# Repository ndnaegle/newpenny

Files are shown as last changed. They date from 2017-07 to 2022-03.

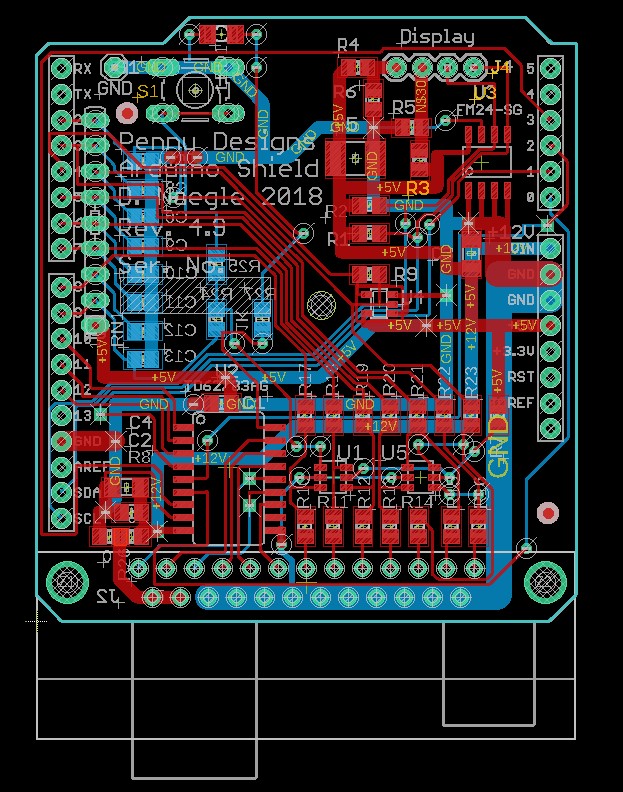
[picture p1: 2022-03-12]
Docs/PennyMan_Ard_R3_Shield_v9.5_all_layers.jpg

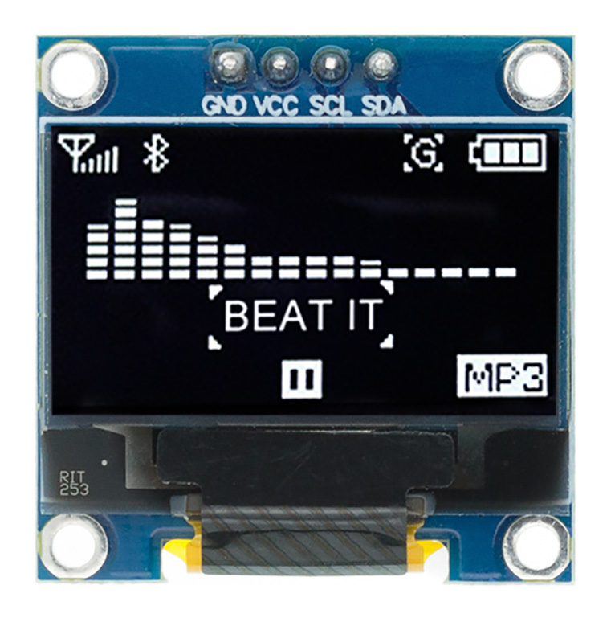
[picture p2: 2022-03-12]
Docs/SSD1306_I2C_DisplayModule.jpg

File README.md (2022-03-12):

# newpenny
This is an Arduino Shield to interface an Arduino to a souvenir making machine.  

The shield contains signal conditioning to give the Arduino more ESD protection as a controller  for the penny press.  

The shield also contains an output level shifter to allow the Arduino to control solid-state relays  that require 12V control inputs.  

The shield also contains a 128x64 pixel display as a debugging aid, and a non-volatile serial memory for storing operational and debug data.  

The shield could serve as a general-purpose I/O conditioning module along with non-volatile memory that could allow the Arduino to retain its
operational state through power failures, by means of appropriate software.

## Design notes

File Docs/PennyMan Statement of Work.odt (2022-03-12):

PennyMan Control Software Description

David Naegle

11 June 2017

The PennyMan machine is a roller press with dies in it that turns a US penny into a souvenir by imprinting it with images or impressions that are typically mementos of the location in which the penny machine resides.

The machine is electrically operated, and is capable of making any one of four impressions by means of a roller die containing four different images located at 90-degree offsets around the circumference of the roller die. The machine works are enclosed in a protective case containing clear windows so that the machine can be observed in operation; the user experience consists in observing the machine making a souvenir for the user, as well as the souvenir itself.

A description of the machine operation follows.

When active, the machine waits for coins to be inserted. The mechanical coin feed ensures that exactly 51 cents, in the form of two quarters and a penny, are required to activate the machine. Once these coins are inserted, the machine prevents any other coins being inserted until the present operation is completed.

The machine waits for the user to select one of 4 impressions to be made on the penny, by means of 4 switches with illustrations of each of the 4 choices for impressions.

Once the user has made a selection, the machine starts the roller mill. Magnetic sensors sense the position of the die, and drop the penny into the mill when the roller die is appropriately positioned for the impression selected by the user in the previous step.

When the penny has been imprinted with the selected image and transformed into souvenir form, it drops down a chute to be picked up by the user.

The machine keeps the roller mill turning until the magnetic sensors indicate it is once again in the “home” position (half-way between impressions 1 and 4). At this point the mill motor is shut off, the coin slot is re-enabled to accept coins, and the cycle starts over, with the machine waiting for another set of coins to be inserted.

The control for the machine comes from an Arduino processor board, equipped with a “shield” which provides connectivity and compatibility with the connectors and wiring harness of the penny machine.

The shield board also provides electrostatic protection and switch “de-bouncing” for signal inputs, as well as voltage level translation on outputs. Outputs level translation is needed to allow the Arduino 3.3V or 5.0 V output signals to drive 12 V solenoids and the motor relay for the machine.

A table of inputs and outputs follows:

Signal | Name | Arduino Pin | | Direction | Notes
1 | Go/No-Go | P0.0 | | In | Go = 0, Halt = 1
2 | Coin Accept | P0.1 | | In
3 | Die #4 | P0.2 | DB25.6 | In
4 | Die #3 | P0.3 | DB25.5 | In
5 | Die #2 | P0.4 | DB25.4 | In
6 | Die #1 | P0.5 | DB25.3 | In
7 | 90-Degree | P0.6 | DB25.2 | In
8 | Home | P0.7 | DB25.1 | Out
9 | Cycle Start | P1.0 | DB25.12 | Out
0 | Solenoid | P1.1 | DB25.10 | Out
11 | Motor Run | P1.2 | DB25.9 | Out
12 | Counter | P1.3 | DB25.7 | Out
13 | | | | Out
14 | | | | Out
15 | | | | Out

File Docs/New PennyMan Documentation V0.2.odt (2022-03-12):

The (Arduino) PennyMan Shield Documentation

D. Naegle

31 October, 2018

1. OLED Display

The PennyMan Arduino interface shield contains provisions for an inexpensive 128x64-pixel Organic Light-Emitting Diode (OLED) display (0.96” SSD1306 128x64 I2C Serial 4Pin Arduino Display Module, available from multiple sellers on eBay, or from Adafruit Industries). Its purpose is to provide continuous indications of what the PennyMan controller is doing (what is the current state of the machine) and the current values of the input and output signals to the PennyMan controller. The PennyMan Shield design accommodates 2 versions of the display module, which differ in the placement of their VCC and GND pins. For VCC on the left-most pin, stuff R4 and R5. For GND on the left-most pin, stuff R3 and R6.

2. OLED Display is optional

Use of the OLED display is optional; the PennyMan Arduino interface shield operates correctly without the shield in place.

CAUTION: Do not plug or unplug the OLED display with power applied to the PennyMan controller. Unplug the power connector to the Arduino processor board, and wait a few seconds before plugging or unplugging the OLED display.

3. Software Interface

The OLED display is accessed through the I2C serial interface provided by the AdaFruit_SSD1306 library.

4. Layout and format of the Display

The display has 3 modes of operation:

· Startup Screen

· Runtime Screen

· Debug Console

These are described as follows

4.1 Startup Screen

The Startup Screen has the banner ‘Pennyman!’, followed by the software revision, optionally followed by a 5-second count-down indicator. The time-out is provided so that the user can get into the Debug Console, in the case that the non-volatile log chip is present on the PennyMan Arduino interface shield. If there is no log chip installed, there will be no count-down; the Startup Screen will be replaced by the Runtime Screen after a few seconds. See Section 4.3, Debug Console, for further information.

4.2 Runtime Screen

The Runtime Screen has 3 lines: Current State, I/O State, and time in current state. The top line indicates the current state of the machine. These are listed below:

State Message Visible in OLED Display | Comment/Explanation
"Start" | Startup State; doesn’t last long enough to be seen on the OLED display. This state sets all output to sane (inactive) values and moves to “Wait for Home”
"Wait for Home" | Runs the Motor, waits for the Home sensor to be active. When Home is sensed, the coin press is in the proper position to begin; this state moves to “Wait for Coin”
"Wait for Coin" | Waiting for the user to insert a penny and quarters to initiate creation of a souvenir. Only in this state, is the Coin-insert mechanism is enabled (Upper Solenoid activated). This is shown by the ‘L’ being a black letter on a white background. (‘L’ stands for ‘Lift Red lever’.) When coins are inserted, the state moves to “Wait for Button”
"Wait for Button" | Wait for the user to select which stamp to impress on the penny. When this selection is made, the state moves to “Position Stamp”
"Position Stamp" | This is a timing state. The Motor is run, and the 90-degree sensor is counted until the press is in the proper position for the user’s selected stamp. At this point, the state moves to “Coin Drop”
"Coin Drop" | Lower Solenoid is activated to drop the penny into the press. Motor continues running in this state. This state lasts for 1 second, then the state moves to “Wait for Finish”
"Wait for Finish" | Motor continues running in this state. This state lasts for 5 seconds, to insure that the souvenir is released from the press into the output chute where the user will pick it up. NOTE: running the motor in this state may cause the press to advance past the ‘Home’ position. This is OK. After 5 seconds, the state moves to “Start”, resetting all outputs inactive and immediately going to “Wait for Home”. As mentioned above, the press may make an entire, extra revolution before the machine is once again in “Wait for Coin” state.
The states below are not part of normal operation; they should not be seen on the Display.
"Invalid" | Software sets the state to ‘Invalid’ before immediately starting the State Machine in the ‘Wait For Home state’ This is just software housekeeping, so the State variable has a known value as soon as possible after the machine powers up.
"Shutdown" | Software defines this state, but it is not used in normal operation. There is no legal way to get to this state. All outputs are set to safe (inactive) values in this state, as part of an “emergency recovery” strategy. From this state, the state goes to “Wait Forever”
"Wait Forever" | This state is intended to trap a runaway machine sequence into a safe, persistent state. As the name implies, we’re stuck in this state until the machine is reset or powered down. If you see this on the Display, you know the machine has been trapped from an unusual and unintended mode of operation. It would be useful to look at the Log, if possible. (See Section 4.3 for instructions on entering the Debug console.)
"Reset" | This was intended to be similar to the “Shutdown” sequence; it attempts to clear the Display, set outputs to safe values, and sets the Watchdog Timer, which will initiate a system reset. It apparently never worked, and is probably not needed. The board will emerge from reset as described above, in “Start”.
"Unknown!" | If the State has any value other than those enumerated above, the Display should show “Unknown!”. Since this is not expected, it should never be seen. It’s unknown if this state would persist on the “Display”. It’s documented here for completeness’ sake. If you see this, you should probably attempt to dump the log, and read the PennyMan source code to figure out what might have happened. Or forget it and move on. Perhaps it would be a good idea to replace the Arduino, the PennyMan shield board, or both, if an unusual state persists.

4.3 Debug Console

The Debug Console must be activated during the 5-second count-down period in the Startup Screen. This is done as follows:

4.3.1 Connect the Arduino to a PC running the Arduino Integrated Development Environment (IDE), using a USB cable.

4.3.2 Under the ‘Tools’ tab in the Arduino IDE, you’ll find a ‘Port’ tab. Select the appropriate COM port (e.g. COM1, COM2, etc.) If you select the wrong COM port, step 4.3.3 will be unsuccessful; you’ll get a warning message about the selected port not being found. Come back to this step and select another COM port.

4.3.3 Under the ‘Tools’ tab, select ‘Serial Monitor’. Look for any error messages that appear in the bottom pane of the Arduino IDE window, indicating failure to open the Serial Monitor with the correct COM port.

4.3.4 Upon successfully opening the Serial Monitor window, select ‘115200 baud’ in the serial speed control pane at the bottom of the Serial Monitor window. The Arduino IDE may remember this from a previous session, so it may not be necessary. NOTE: opening the Serial Monitor window resets the Arduino hardware, forcing it to start from scratch. The Log file, if any, will be unaffected by resets. See section X.X for more information on using the log file.

4.3.5 Position the PC’s cursor in the uppermost pane of the Serial Monitor window (to the left of the ‘Send’ button) and type a ‘d’ but DON’T HIT RETURN yet.

4.3.6 Press the reset button on the Arduino board (NOT the pushbutton on the PennyMan Arduino interface shield board (the top board in the stack). The Arduino reset button is on the lower (main Arduino) board, next to the USB connector. This will initiate the Startup screen and the 5-second time-out period.

4.3.7 Hit ‘Enter’ (or ‘Return’ depending on the labeling of your PC keyboard) or click ‘Send’ on the Serial Monitor window within the 5-second time-out. Either of these actions will send the previously typed ‘d’ to the Arduino board. The OLED Display will show “Debug console running’. The Serial Monitor should also show a list of commands that can be typed from the top pane of the Serial Monitor in Debug mode, to manage the Log file.

4.3.8 In the Debug Console, there are 3 commands, ‘d’, ‘c’, and ‘x’. ‘d’ dumps the log file to the Serial Monitor. Dumping the log file does not erase it. However, you may wish to preserve the log file in a human-readable form, by selecting the dumped text from the Serial Monitor central pane, copying it (with ‘ctrl-C’) and pasting it to your favorite text editor. From there, the file can be saved or processed as needed. ‘c’ clears the log file. There is no recovering from this! ‘x’ exits Debug Mode and boots back into the Runtime mode and screen.

5. Using the Serial Monitor.

If connected to a PC via USB to the Arduino IDE with a Serial Monitor opened as described above, the PennyMan Arduino Controller prints the same messages to the Serial Monitor as to the Log File. These messages have the following format: <timestamp> of the form hours.minutes.seconds.milliseconds, followed by the separator ‘->’, followed by a description of actions occurring at that timestamp. There may be multiple lines of output. It’s not completely clear which timestamp such unlabeled lines are associated with. However, if there are multiple un-timestamped lines, they all occurred essentially simultaneously, some time after the nearest-preceding time stamp, and before or at the subsequent time stamp. NOTE: the timestamp does not come from the Arduino; it’s the PC’s system time. Showing the Timestamp can be controlled by checking or un-checking the ‘Show Timestamp’ box at the bottom of the Serial Monitor. Similarly, ‘Autoscroll’ affects the screen by being checked or unchecked. In general, the default settings at the bottom of the Serial Monitor are best (except for the Baud rate, which must be manually set to 115200 baud in order to get non-gibberish messages to appear on the Serial Monitor)

It may be useful to clear the Serial Monitor window; this may be done by clicking the ‘Clear output’ button at the lower-right of the Serial Monitor screen.

NOTE: It is possible (and very convenient) to exercise the Arduino & PennyMan shield by connecting them to the PC with the USB cable (no separate 12-volt power supply is needed). You don’t need to connect the DB-25 connector to the PennyMan wiring harness, either. You can simulate the inputs using the Serial Monitor, by typing a character into the Serial Monitor, and hitting the ‘Send’ button or simply hitting ‘Enter’ on the keyboard. NOTE: not all characters will be recognized in all states. Carefully read the table below, to determine the characters expected (and the only ones allowed) in any given state.

NOTE: although it is possible to program the PennyMan software into an Arduino without a PennyMan shield board attached, (see section 6 for programming instructions) the PennyMan program will NOT run reliably on the Arduino without a PennyMan shield board attached. This is because the pull-up resistors which keep the input signals at known (sane) levels are on the PennyMan shield; without the shield installed, the inputs are “floating”. They may be High (inactive), Low (active) or anywhere in between. Random cosmic rays can change the state of floating input pins, and the Arduino will interpret the floating inputs in ways that lead to chaotic operation. Save yourself a lot of confusion; always us a PennyMan shield, even when you’re only connected to the PC.

State Message Visible in OLED Display | Legal/Expected Characters from Serial Monitor
"Start" | n.a. (no user input expected in this state)
"Wait for Home" | h
"Wait for Coin" | c
"Wait for Button" | 1, 2, 3, or 4
"Position Stamp" | 9. (you’ll need to send a ‘9’ 1, 2, 3, or 4 times, depending on which button you selected, above.)
"Coin Drop" | n.a. (no user input expected in this state)
"Wait for Finish" | n.a. (no user input expected in this state)
The states below are not part of normal operation; they should not be seen on the Display. If you get any of the states below, it may indicate an Arduino board that is beginning to fail; replace it and try again.
"Invalid" | n.a. (no user input expected in this state)
"Shutdown" | n.a. (no user input expected in this state)
"Wait Forever" | n.a. (no user input expected in this state)
"Reset" | n.a. (no user input expected in this state) Note, however, that opening the Serial Monitor causes a reset, as does changing the baud rate (e.g., to something other than 115200 and changing it back to 115200 again.)
"Unknown!" | n.a. (no user input expected in this state)

6. Programming the Arduino.

Obtain the PennyMan source code from GitHub as follows:

Go to

https://github.com/ndnaegle/newpenny

There are 2 directories under this project, Docs and main. Docs contains design information and documentation, including this file. main contains the Arduino code for the project.

The use of GitHub is beyond the scope of this document, but there are plenty of tutorials on the Web.]

Further note: The newpenny Arduino sketch (Arduino programs are called 'sketches') requires, in addition to all the files in the newpenny GitHub repository, the AdaFruit SS1306 display libraries and the AdaFruit graphics library. To get the SS1306 library, go to this site: https://github.com/adafruit/Adafruit_SSD1306 and click 'Clone or Download'. Select 'Download ZIP file'. That should put a copy of the Zip file in your Downloads directory if you're running Windows. The process is similar for MacOS. To get the AdaFruit Graphics library, go to this site: https://github.com/adafruit/Adafruit-GFX-Library and click 'Clone or Download'. Select 'Download ZIP file'. That should put a copy of the Zip file in your Downloads directory if you're running Windows. Jon modified the FRAM library from AdaFruit, but didn't debug it sufficiently to recognize any FRAM but the ones from Fujitsu. I think a better library is available here: https://github.com/adafruit/Adafruit_FRAM_I2C although some coding work would have to be done to insure the routines Jon wrote for his library can be replaced by those in FRAM_I2C. The advantage is that much more testing has been done with FRAM_I2C for supporting many types of FRAM.

Look at the documentation for the Arduino IDE about loading libraries. Basically, from inside the Arduino IDE, you can load additional libraries. There is a dialog for navigating to the ZIP file containing the library and opening it. Once the Arduino IDE has opened the ZIP file containing the library, it will be accessible to programs wishing to use it; you won't get compile errors complaining about missing libraries.

Once you have the PennyMan source on your PC (mine is at C:\Users\Naegle\Documents\GitHub\newpenny) you start up the Arduino IDE (downloadable from the Web; google for details), navigate to …\GitHub\newpenny, and open main.ico. This should give you the whole source. You can compile the code to check it by clicking on the check-mark box in the upper-left of the Arduino IDE. You can compile and upload the code to a connected Arduino board (see above for connecting the board with a USB cable) by clicking on the right-arrow button in the Arduino IDE. Note any diagnostic messages in the bottom of the IDE; they will tell you if you succeeded in programming the Arduino, and if not, what may have gone wrong. Full instructions on compilation and uploading are beyond the scope of this document, but are well-documented on the Web.

7. Weird Stuff it’s well to watch.

7.1 Pin D4 (Coins Accepted) was hard to “pull down” (bring to an active, (LOW) state) on the Arduino board. I tried a couple of different Arduinos, with the same result, but never found out the reason why this input didn’t behave like the others. I used a strong buffer the 74AHC1G125, to force the Arduino D4 pin LOW when the coin drop was active. I have designed in a “stuffing option” to the shield board, such that the 74AHC1G125 buffer can be eliminated and a zero-ohm bypass resistor installed (R9), which will be cheaper and SHOULD work correctly. I tried this experiment with the latest (Rev 4.8) version of the PennyMan shield, and the buffer is still required. NOTE: DO NOT install BOTH R9 and the 74AHC1G125, install one or the other. Next step: try explicitly setting Arduino pin D4 as an INPUT. Jon took advantage of the published behavior of the Arduino IDE to set pins to be inputs by default. But what if pin D4 is set up strangely. (No Google searching revealed any problems with default-input behavior specific to pin D4, and Jon maintains it should be a regular input. I've minutely searched the schematics and examined the Arduino board layout to find if there's anything else connected to D4 that would change its behavior. Still a mystery, so for now, we'll rely on the fact that we have the buffer, and hope its use doesn't stress the Arduino pin. Somewhere a lot of current is getting shorted to ground by the 74AHC1G125 buffer. Fortunately, the buffer is only active for a second or so (for as long as the coin slide is pushed in), so the stress is not continuous over time.

7.2 I had hoped to increase the flexibility of the PennyMan shield (for other projects) by including a mechanism to bring +12V out of the DB-25 connector. To do this I “stole” a couple of ground pins on the DB-25, making them programmable as +12V or “floating”. However, I found that the Upper Solenoid solid state relay uses a ground on the harness which is connected to one of the DB-25-pins I “stole”. Therefore, it is necessary to connect these pins to ground. This may be done on the board, with a zero-ohm surface-mount resistor (R8) placed so that it shorts the output pins to the ground side of C2. This is not really ideal, however. An easier way is to simply take a short piece of wire and short DB25 pins 25 and 24 to pin 23.

7.3 The SSD1306 OLED display is available with two different pin placements for +5V and GND. In order to accommodate the use of both types (and thus keep costs down on the board, by buying whichever version happens to be cheaper at the moment) I have designed zero-ohm resistors (R3, R4, R5, R6) to connect the two power pins on the OLED display to the appropriate power and ground. Two of these resistors MUST be left un-stuffed, in order to avoid a power-to-ground short circuit, which will damage both the PennyMan Shield and the Arduino board. Plugging in a wrong-style OLED display will also damage the display and maybe the shield and Arduino. It might be prudent to select one or the other type of display, so that you don’t have to be so careful to mate the proper display with the proper placement of these resistors.

7.4 The pushbutton on the Shield was intended as an additional, generic input. It is currently unused, but goes to an Arduino input (D9) which could be defined in inputs.h and used in some way. But without writing software, this pushbutton does nothing, and could be left un-stuffed on the board to reduce cost and speed up assembly of the shield.

7.5 I have put a ground pin close to the pushbutton switch. This is a convenience for debugging the board; it’s often handy to have an easy place to ground an oscilloscope probe or multi-meter probe, when making measurements. It is not really needed during normal operation, and could be eliminated without any ill effect (until you need to connect a ground to the board when you’re debugging something. At that point, you could do a field-soldering job and put in a wire or a pin in that location.)

7.6 There are several flavors of FRAM log chip that all fit the pin-out of the board. The FRAM_I2C.cc module attempts to read the size of the chip installed, and sets up the FRAM according to the size it finds. However, the cheapest versions of the FRAM chip (24C04) do not have a manufacturer’s ID like some of the more modern (more expensive) chips. The Fujitsu 256K chip costs about $4-6, whereas the Cypress Semi 24C04 costs about a dollar. Currently the FRAM_I2C module does not correctly set up the 24C04. This leads to strange behavior in Debug Mode, when the software believes there’s a log chip, but it doesn’t work correctly because it’s not properly set up, because it wasn’t recognized because it doesn’t have a manufacturer’s ID. We can solve this by only using the Fujitsu parts. But it’s not a very elegant solution.

7.7 The current implementation of the FRAM dedicates the entire chip to the Log file. There ought to be a way of reserving the first few locations in the chip for use as counters. This would involve some changes (probably minor) to the way the log addressing is done: set the initial log pointer to just above the reserved space for the counters, set the wrap-around routine to respect the reserved locations and avoid clobbering them when it wraps the log address around. And, of course, there needs to be some new FRAM routines written to use the reserved locations as Counters. NOTE: there is no (legacy) counter function implemented on the latest (Rev 4.8) version of the PennyMan shield.

7.8 There will need to be some minor changes to the FRAM_I2C code to recognize that the Log chip is absent (un-stuffed), in order to properly disable the logging and the debug console when no chip is present. The logging FRAM chip is the most expensive one remaining on the PennyMan shield board, and it’s not required for normal operation of the PennyMan system, according to Kristen and Brett.

  9. I made a couple of designs for latching the “red lever” (coin-accept enable) so that the upper solenoid (coin-accept enable) wouldn't have to be continuously activated. Kristen says it's a known failure mechanism: eventually, the upper solenoid burns out and has to be replaced, despite using an expensive solenoid that is, per it's specs, rated for continuous activation. My latch is mechanical, spring loaded, and holds the red lever up until the coin slide is pushed in. I built a prototype of my first design, and it appears to work as designed. Unfortunately, with the red lever lifted, it appears that the coin slide can be pushed in without coins in it, which will unlatch my latch, preventing pushing in the coin slide, whether or not there are coins in it. (Apparently the Coins-accepted magnetic switch isn't activated unless the coin slide is pushed in AND it contains coins.) So, my scheme to mechanically latch up the red lever and unlatch it with the coin slide, apparently won't work with the current coin slides.
    1. I then investigated latching solenoids, so that the state machine could control the latching and unlatching of the red lever. I did find such solenoids (see the s-73-31 from TLX Technologies, tlxtech.com, which is activated from 4 AA batteries.) This means the s-73-31 solenoid doesn't need 120V AC and a solid-state AC relay to activate it; the PennyMan shield driver should be sufficient to directly activate it, eliminating the Upper Solenoid solid-state relay. Upon further consideration, I realized that this solenoid could replace the red lever entirely; just mount the solenoid so that in the extended, latched position, it blocks the coin slide from being pushed in, just like the red lever does now. In the retracted, latched position, the solenoid allows the coin slide to be pushed in. Use of this scheme requires another output from the Arduino/PennyMan shield assembly, and additional wiring in the DB-25 conntector and wire harness, because the latching solenoid has one wire for extending, and one wire for retracting. Fortunately, version 4.8 and subsequent versions of the PennyMan Shield board have two additional, unused outputs which are buffered like all the original outputs. All that's required to use these is to define the pins in the Arduino newpenny sketch, and modify the state machine in the sketch to use the latching solenoid.
  10. Realizing that the Upper solenoid didn't require a solid-state relay led me to wonder if a different solenoid could be found for the coin-drop solenoid, which could be directly operated by the PennyMan Arduino shield. This would not be a new output, it would simply re-purpose the existing Coin-Drop output. This would not require any code changes, but it WOULD eliminate another solid-state relay. The only remaining solid-state AC relay would be the one for the Motor, and that one is necessary, because the motor requires lots of power.
  11. I found a 3D printed mounting fixture for the Arduino Uno. I had it printed out on 3DHub. Unfortunately, the cost of 3D printing in low volumes is relatively high; the mount cost about $20.00 with printing and shipping. BUT I then got the idea to create a silicone mould from the 3D printed part, and do polyurethane casting to produce copies of the mount. I uploaded the 3D file to another site and found that the volume of the mount is 15,00 mm3. 2 pints of polyurethane resin (less 20% of the volume, to account for inability to scrape every last mm3 from the mixing cups) is sufficient to make about 46 mounts. I figure that, with $22.00 for a 2-pint sample kit of the polyurethane casting resin, $29.00 for the silicone moulding compound, and $20.00 for the 3D printed original mount, divided by 46, is less than $1.60 per mount. That's probably acceptable, assuming the cast copies are as dimensionally accurate as needed for this application. The labor to cast up 46 of these should not be any worse than the labor to assemble all the fiddly spacers, etc., for mounting the Arduino board without the plastic mount. In use, the mount requires 2 to 4 #6 panhead screws to affix it to the wooden PennyMan cabinet, plus one #4 panhead screw to secure the Arduino board within the mount. The PennyMan Shield will be attached to the Arduino board through its pins which mate with the sockets on the Arduino board, and should not require any additional mechanical mounting.
  12. I've been thinking about how to improve the engraving of the dies in the penny press. It seems to me that engraving a graphite picture, using computer-numeric-control (CNC), then using the graphite as an Electrical Discharge Machining (EDM) electrode, would largely automate the engraving of the dies. I don't know if this is cheaper than ordering it done as it is now, but it might be a way of getting anything you can get drawn as a black-and-white image, easily and quickly onto a stamping die. The nice thing about EDM is that you can pre-harden the roller, then EDM engrave it, without changing its hardness properties. That would seem to be important for long die life.
  13. I have uploaded a version 4.9 of the Pennyman Arduino Shield. This version differs from version 4.8 in that it has a generic LED driven by the Arduino D10 line. Without additional software, this LED does nothing at present. I had some notion of using the LED in situations where the OLED display was not present.
  14. I had an idea to create a test environment for the PennyMan Arduino Shield that would simulate the signal environment of an actual PennyMan machine without using an actual machine with its bulk and expense. I have the wiring harnesses set up, but I did not yet succeed in making the motor behave as a real motor does (with its inertia and coasting behavior). I also need further refinements on the position sensing mechanism to create the signals that tell the Shield when the selected one of 4 die images is in position for the penny to be dropped into the press. Use of such a test station might be a way to automate lifetime testing of the Shield.

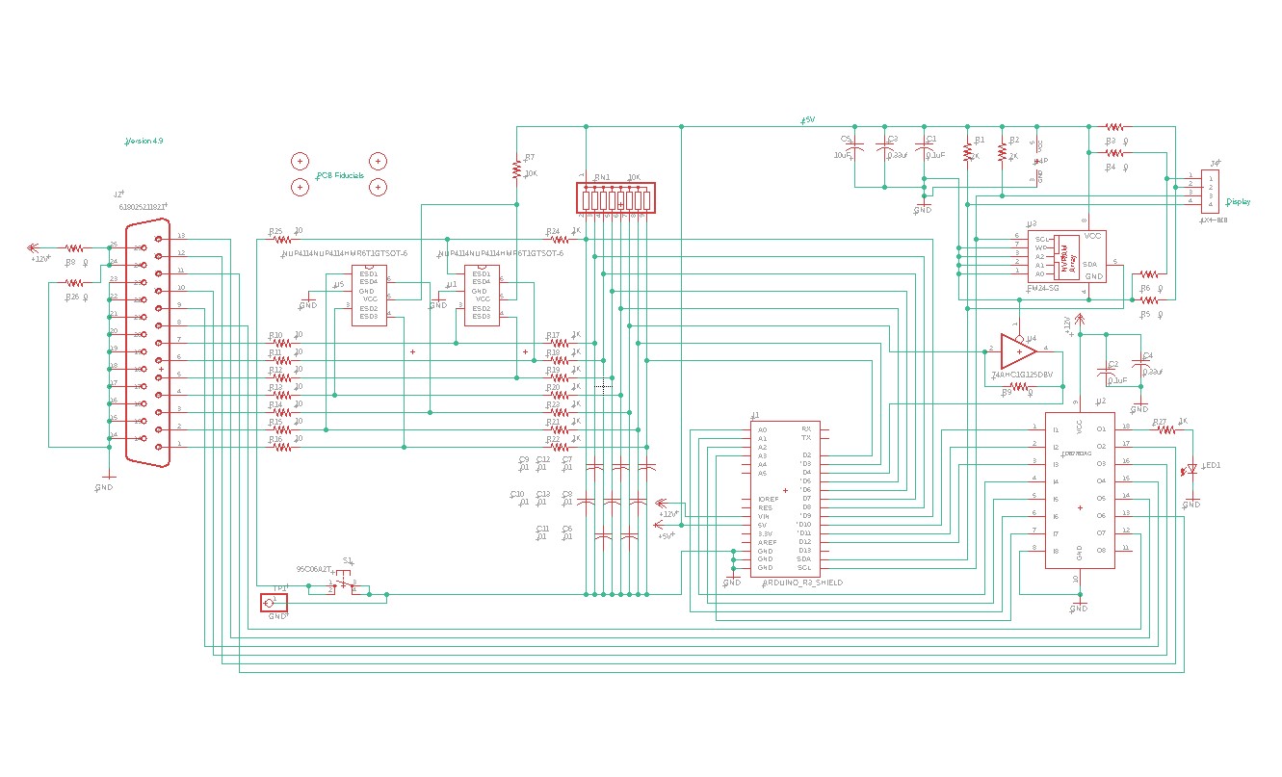
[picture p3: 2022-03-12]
Docs/PennyMan_Ard_R3_Shield_v9.5_schematic.jpg

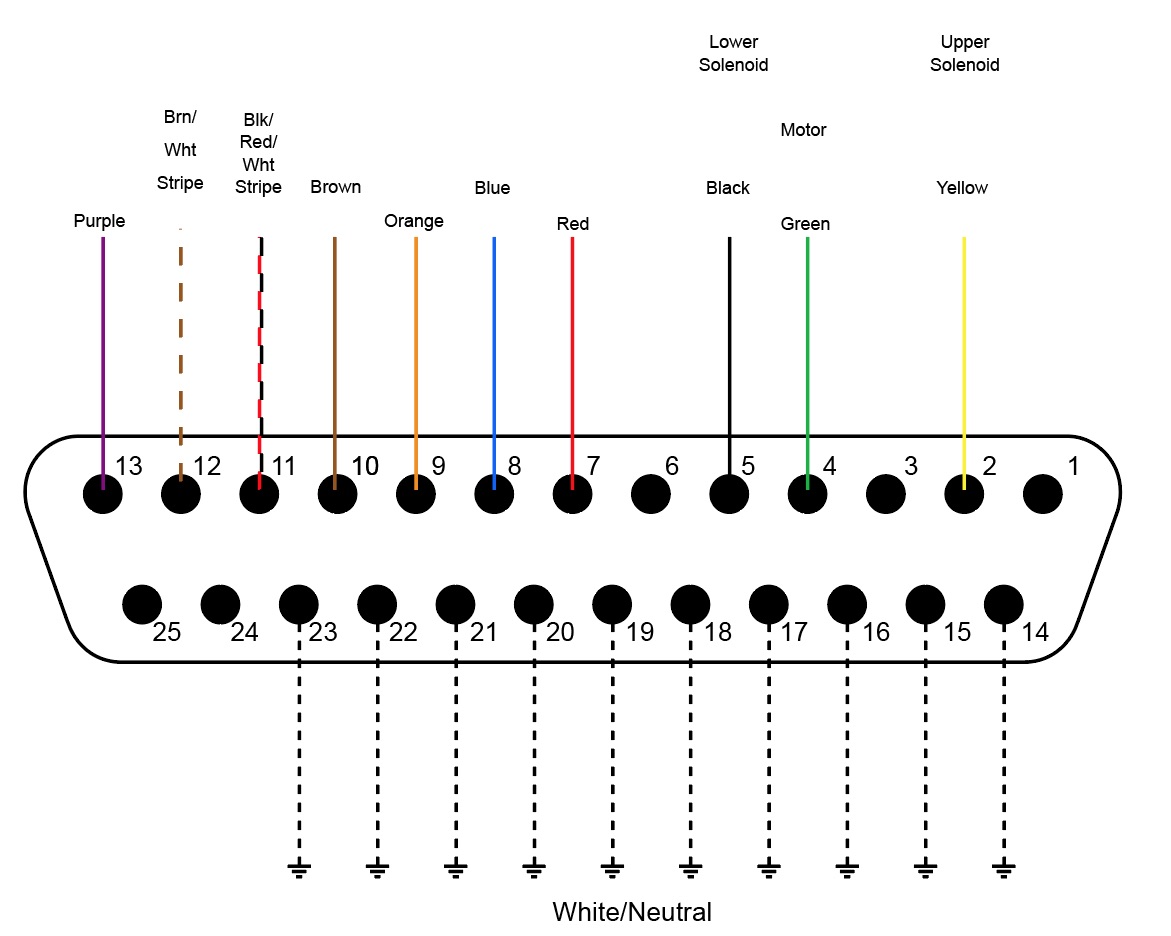
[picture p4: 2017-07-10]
Docs/DB25 Connector.jpg

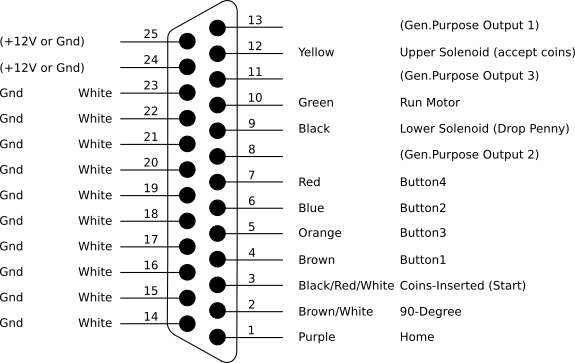
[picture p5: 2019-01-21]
Docs/PennymanDB25Connector_V2.png

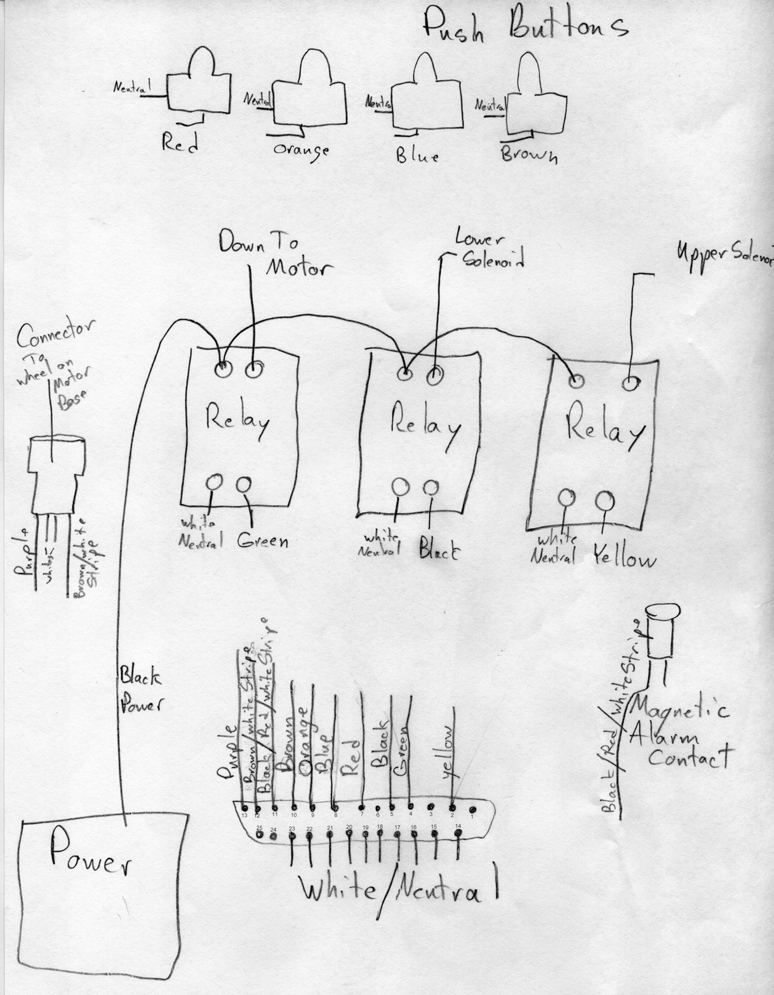
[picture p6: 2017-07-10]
Docs/HarnessDiagram.jpg

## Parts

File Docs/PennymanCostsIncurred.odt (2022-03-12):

9/18/2016 $ 55.81 PCBCART order #518778

9/18/2016 $ 23.34 eBay: 6 Arduinos

9/19/2016 $101.83 eBay:

10 DB25's @ $1.223 $ 12.23

10 MAX6818's @ $6.00+$4.90 $ 64.90

10 TD62783's @ $1.134 $ 11.34

100 0.33uF's @ $0.0449 $ 4.49

2 solder flux @ $2.45+2.98 $ 7.88

100 0.1uF's @ $0.0099 $ 0.99

=====

$101.83

11/25/2016 $ 21.01 250 Female connectors @ $0.06572 $ 16.43

Tax & Shipping $ 4.58

======

$ 21.01

11/27/2016 $ 73.31 PCBCART order #521453

6/27/2017 $ 15.75 3ea OLED displays (ebay) $ 15.75

7/4/2017 $ 73.31 PCBCART order #530223

7/10/2017 $ 16.10 5ea OLED displays (ebay) $16.10

7/10/2017 $ 31.40 10ea OLED displays (ebay) $31.40

7/12/2017 $ 10.31 35 Tactile Switches @ $0.152 $ 5.32

Tax & Shipping $ 4.99

=====

$10.31

7/20/2017 $ 5.67 5000ea 0805 pkg 0 ohm resistors $ 5.67

7/21/2017 $ 4.74 50ea 1812 pkg 10uf Capacitors $ 4.74

7/22/2017 $ 0.99 100ea 0805 pkg 0.1uF Capacitors $ 0.99

20/7/2017 $ 53.66 Mouser

Screws, spacers, 4-pin sockets

7/30/2017 $ 77.51 PCBCART order #531272

26/8/2017 $ 1.72 10 magnetic reed switches $ 1.72

1/5/2018 $ 99.89 PCBCART order #537409

8/29/2018 $ 92.54 PCBCART order #546364

?/?/2017 $? FRAM

19/8/2017 $ 44.09 100 SMT LEDs @.391 $39.10

Tax & Shipping $ 4.99

=====

$44.09

5/1/2018 $ 17.59 100 NC7SZ125M5X Buffer @ $0.126 $12.60

Tax & Shipping $ 4.99

=====

$17.59

8/11/2018 $ 33.32 8 OLED displays @3.24 $24.92

Shipping & Handling $ 7.42

=====

$33.32

8/?/2017 $300.00 Software Development – pd to Christopher Thomason

8/27/2018 $ 32.87 50 NUP4114 ESD diodes @ $0.533 $26.65

Tax & Shipping $ 6.22

=====

$32.87

8/31/2018 $ 39.90 1 reel 0805 10-ohm chip resistor (ebay) $ 39.90

8/31/2018 $ 22.50 2 ea 5x 100K resistor network (ebay)

8/31/2018 $ 6.15 100ea 0805 0.01uF smt capacitors (ebay) $ 6.15

10/26/2018 $ 5.57 2ea 5x 10K resistor network (ebay) $ 5.57

11/07/2018 $ 61.77 DigiKey:

10 256K FRAMs @ $3.832 $38.32

20 0.1” Connector Headers @ $0.454 $ 9.08

Tax & Shipping $14.37

=====

$61.77

11/17/2018 $ 4.99 5 meters music wire 0.022” dia (ebay) $ 4.99

11/29/2018 $ 9.98 2ea 5 meters music wire 0.022” dia (ebay) $ 9.98

11/22/2018 $ 44.95 eBay: 5 Arduinos @ $8.99 ea.

11/21/2018 $ 20.69 3D Hubs: Arduino Mount, 1 @ 6.69 + 4.00 startup + 10.00 shipping

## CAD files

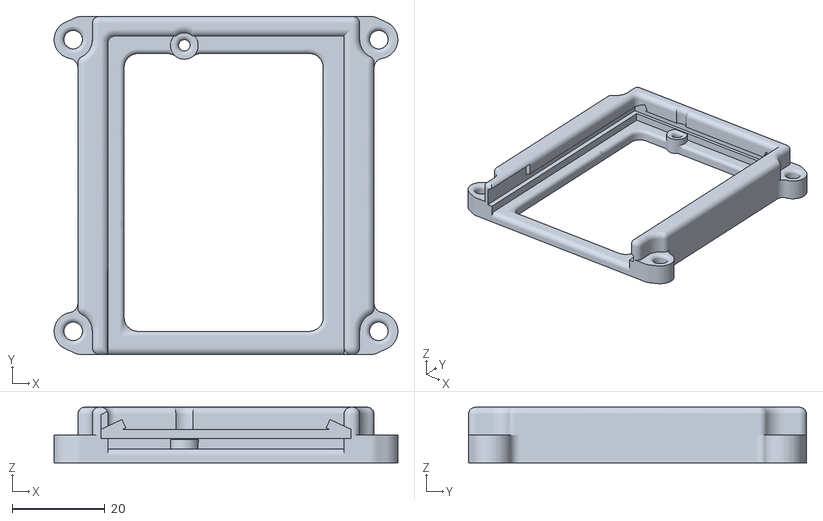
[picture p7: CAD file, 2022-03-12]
Docs/Arduino_mount1_repaired.stl
74.2 x 73.0 x 12.0

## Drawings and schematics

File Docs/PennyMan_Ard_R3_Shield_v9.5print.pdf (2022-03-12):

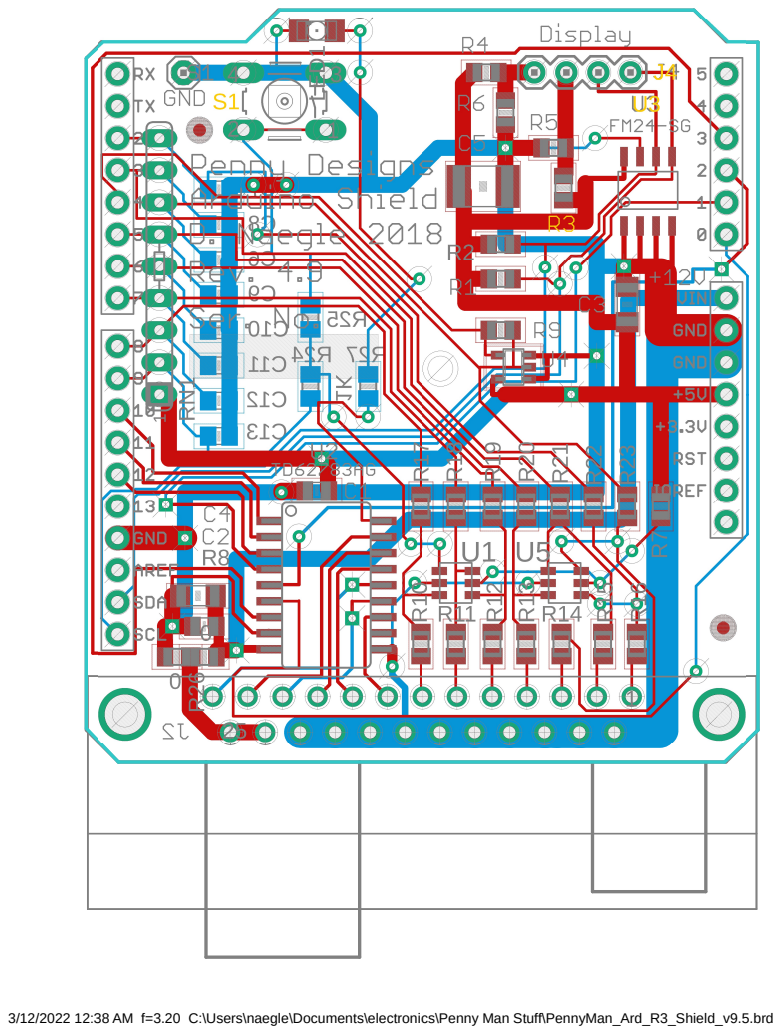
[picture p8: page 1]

3/12/2022 12:38 AM f=3.20 C:\Users\naegle\Documents\electronics\Penny Man Stuff\PennyMan_Ard_R3_Shield_v9.5.brd

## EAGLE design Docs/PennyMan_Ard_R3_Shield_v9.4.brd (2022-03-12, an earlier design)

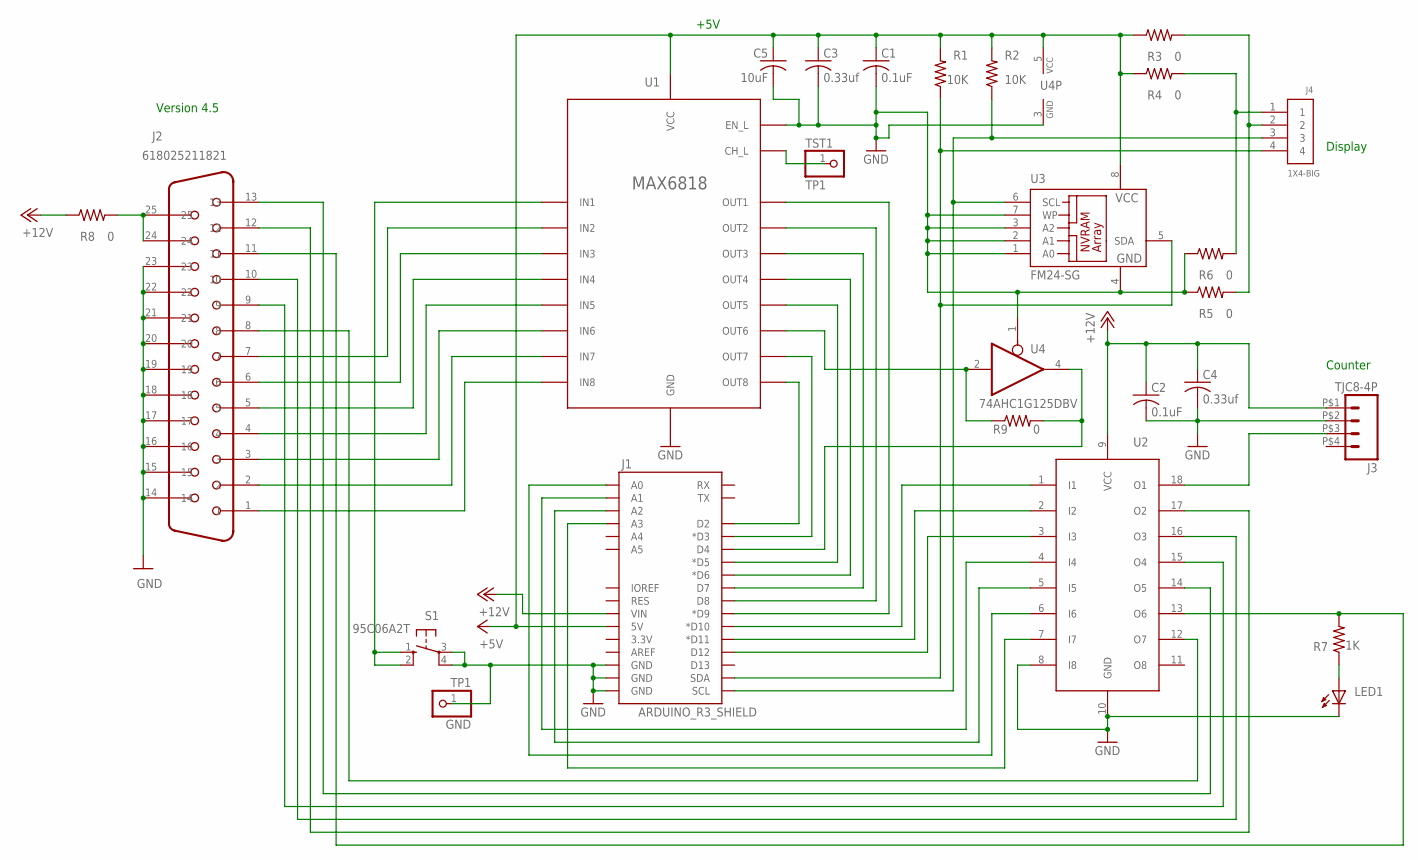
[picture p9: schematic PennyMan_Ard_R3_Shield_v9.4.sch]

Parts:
C1, C2: 0.1uF; C0805
C3, C4: 0.33uf; C1206
C5: 10uF; C1812
GND: TP1; 1X01
J1: ARDUINO_R3_SHIELD; UNO_R3_SHIELD
J2: 618025211821
J3: TJC8-4P
J4: 1X4-BIG; 1X04-BIG
LED1: LEDSML0805; SML0805
R1, R2: 10K; R0805
R3, R4, R5, R6, R8, R9: 0; R0805
R7: 1K; R0805
S1: 95C06A2T; B3F-10XX
TST1: TP1; 1X01
U1: MAX6818; SSOP20
U2: TD62783AG; SOP18
U3: FM24-SG; SO8
U4: 74AHC1G125DBV; SOT23-5

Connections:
+5V: C1.1, C3.1, C5.1, J1.5V, R1.2, R2.2, R3.1, R4.1, U1.VCC, U3.8 (VCC), U4.5 (VCC)
+12V: C2.1, C4.1, J1.VIN, J3.P$1 (1), R8.1, U2.9 (VCC)
GND: C1.2, C2.2, C3.2, C4.2, C5.2, GND.1, J1.GND@0 (GND), J1.GND@1 (GND), J1.GND@2 (GND), J2.14, J2.15, J2.16, J2.17, J2.18, J2.19, J2.20, J2.21, J2.22, J2.23, J3.P$2 (2), LED1.C, R5.1, R6.1, S1.3, S1.4 (P1), U1.EN_L, U1.GND, U2.8 (I8), U2.10 (GND), U3.1 (A0), U3.2 (A1), U3.3 (A2), U3.4 (GND), U3.7 (WP), U4.1 (OE), U4.3 (GND)
unnamed: J2.1, U1.IN8
unnamed: J2.2, U1.IN7
unnamed: J2.3, U1.IN6
unnamed: J2.4, U1.IN5
unnamed: J2.5, U1.IN4
unnamed: J2.6, U1.IN3
unnamed: J2.7, U1.IN2
unnamed: J1.D9 (*D9), U1.OUT1
unnamed: J1.D8, U1.OUT2
unnamed: J1.D7, U1.OUT3
unnamed: J1.D6 (*D6), U1.OUT4
unnamed: J1.D5 (*D5), U1.OUT5
unnamed: J1.D3 (*D3), U1.OUT7
unnamed: J3.P$3 (3), U2.18 (O1)
unnamed: J1.D2, U1.OUT8
unnamed: J1.A0, U2.6 (I6)
unnamed: J1.D10 (*D10), U2.1 (I1)
unnamed: J1.D11 (*D11), U2.2 (I2)
unnamed: J1.D12, U2.3 (I3)
unnamed: J1.A1, U2.4 (I4)
unnamed: J2.12, U2.17 (O2)
unnamed: J2.10, U2.16 (O3)
unnamed: J2.9, U2.15 (O4)
unnamed: TST1.1, U1.CH_L
unnamed: J1.SCL, J4.3, R2.1, U3.6 (SCL)
unnamed: J2.13, U2.14 (O5)
unnamed: J4.1, R4.2, R6.2
unnamed: J1.SDA, J4.4, R1.1, U3.5 (SDA)
unnamed: J4.2, R3.2, R5.2
unnamed: J1.D4, R9.2, U4.4 (O)
unnamed: J1.A2, U2.5 (I5)
unnamed: LED1.A, R7.1
unnamed: J2.11, R7.2, U2.13 (O6)
unnamed: S1.1 (S), S1.2 (S1), U1.IN1
unnamed: J1.A3, U2.7 (I7)
unnamed: J2.8, U2.12 (O7)
unnamed: J2.24, J2.25, R8.2
unnamed: R9.1, U1.OUT6, U4.2 (I)

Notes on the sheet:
+5V
Version 4.5
Counter
Display

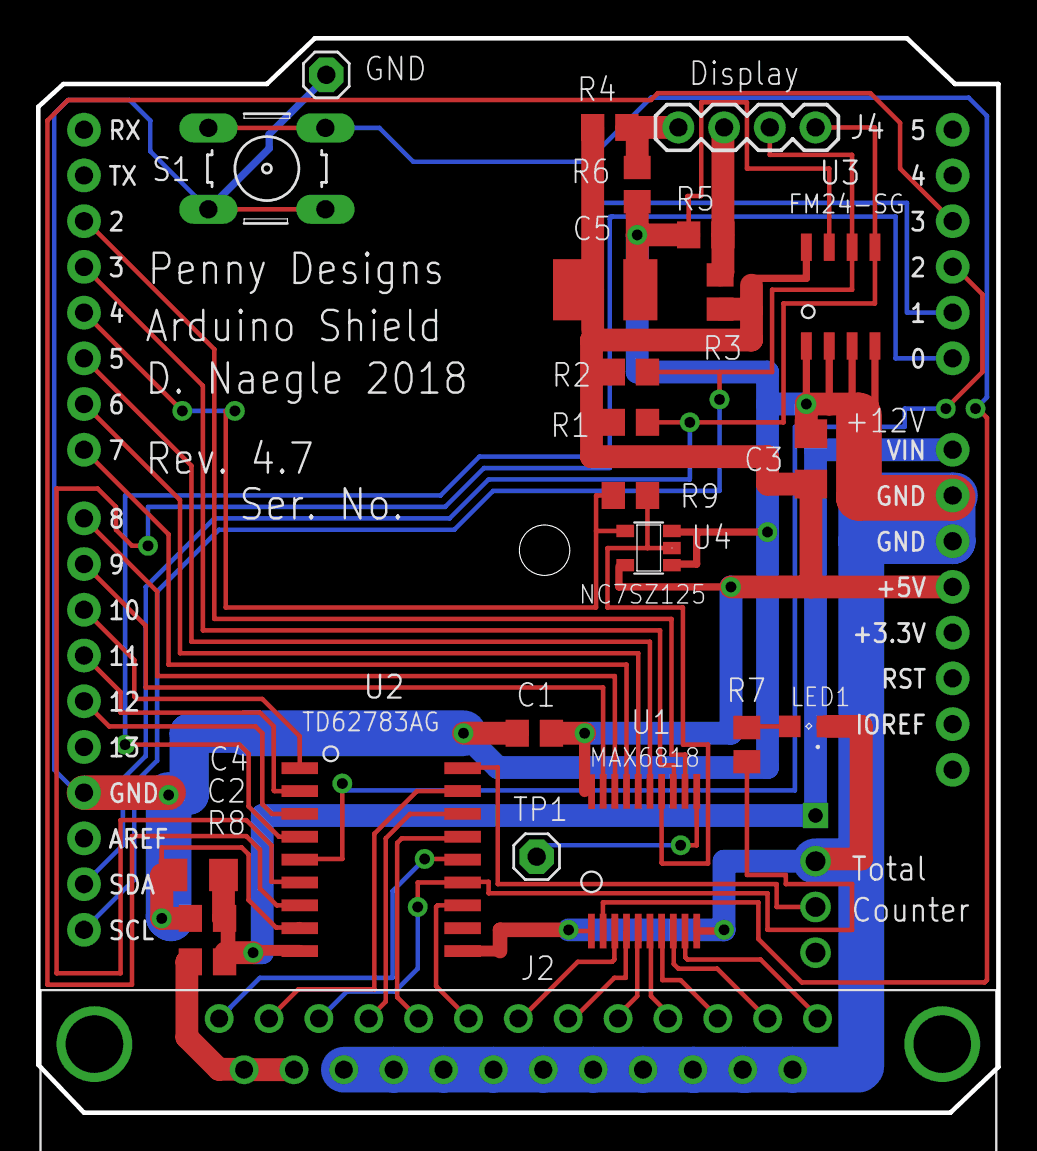
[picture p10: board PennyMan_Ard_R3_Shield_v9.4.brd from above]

Board: 2 copper layers, 53.3 x 59.7 mm, 26 parts (0 on the bottom side), 41 nets.

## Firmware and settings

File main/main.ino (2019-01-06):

// Main.ino
//  Main source file for newpenny project
//  June 2017

// Libraries used:
//  AdaFruit GFX
//  AdaFruit SSD1306

#include <avr/wdt.h>

#include "main.h"
#include "log.h"
#include "input.h"
#include "console.h"
#include "display.h"
#include "output.h"
#include "pinouts.h"

// Globals
int theState = INVALID_STATE;
int haveFRAM = NO_FRAM;

const char* dumpState(int state) {
    const char* pTag = NULL;
    switch (state) {
      case INVALID_STATE: pTag = "Invalid"; break;
      case START_STATE: pTag = "Start"; break;
      case WAIT_FOR_HOME_STATE: pTag = "Wait for Home"; break;
      case WAIT_FOR_COIN_STATE: pTag = "Wait for Coin"; break;
      case WAIT_FOR_BUTTON_STATE: pTag = "Wait for Button"; break;
      case STAMP_SELECTOR_STATE: pTag = "Position Stamp"; break;
      case COIN_DROP_STATE: pTag = "Coin Drop"; break;
      case WAIT_FOR_STAMP_FINISH_STATE: pTag = "Wait for Finish"; break;
      case SHUTDOWN_STATE: pTag = "Shutdown"; break;
      case RESET_STATE: pTag = "Reset"; break;
      case FOREVER_STATE: pTag = "Wait Forever"; break;
      default: pTag = "Unknown!"; break;
    }
    return pTag;
}

void setup() {
    Serial.begin(115200); // be sure to set '115200 baud' in Serial Monitor window
    while (!Serial)
        ;

    // Initialize FRAM logging
    theLog.init();
        
    // initialize our screen
    initDisplay(VERSION);
    
    // Modes for pins assumed to be INPUT so we don't set modes for inputs

    // Initialize pin input emulation via serial (input.cpp)
    initSerialKeys();

    // Set the mode for the output pins
    pinMode(outputCounterPin, OUTPUT);
    pinMode(outputCoinDropPin, OUTPUT);
    pinMode(outputMotorRunPin, OUTPUT);
    pinMode(outputRedLeverLiftPin, OUTPUT);

    // Give the user a chance to start the debug console
    debugConsole();

    // make sure hardware is in a sane state
    fdump("\n\nStarting up at %lu ticks\n", millis());
    fdump("Setting pins to a sane state\n");
    outputRedLeverLift.write(LOW);
    outputMotorRun.write(LOW);
    outputCoinDrop.write(LOW);
    outputCounter.write(LOW);

    // Start at reset state
    fdump("Starting state machine\n");
    gotoState(START_STATE);
}

int stamp = 0;
boolean edgeDetect = false; 

void loop() {
    static unsigned long int countdown = 0;
    
    switch (theState) {
        
    case START_STATE:
        outputRedLeverLift.write(LOW);
        outputMotorRun.write(HIGH);
        inputHome.start();
        inputReset.start();
        gotoState(WAIT_FOR_HOME_STATE);
        break;

    case WAIT_FOR_HOME_STATE:
        if (inputHome.read() == ACTIVE) {
            fdump("Motor reached home position\n");
            outputMotorRun.write(LOW);
            outputRedLeverLift.write(HIGH);
            gotoState(WAIT_FOR_COIN_STATE);
            countdown = millis();
      }
        break;
        
    case WAIT_FOR_COIN_STATE:
        if (inputCoinAccept.read() == ACTIVE) {
            fdump("Coin has been accepted\n");
            outputRedLeverLift.write(LOW);
            inputButton1.start();
            inputButton2.start();
            inputButton3.start();
            inputButton4.start();
            gotoState(WAIT_FOR_BUTTON_STATE);            
        }
        break;
        
    case WAIT_FOR_BUTTON_STATE:
        if (inputButton1.read() == ACTIVE) {
            fdump("Button 1 has been pressed\n");
            stamp = 1;
            outputMotorRun.write(HIGH);
            input90Degree.start();
            gotoState(STAMP_SELECTOR_STATE);
        }
        else if (inputButton2.read() == ACTIVE) {
            fdump("Button 2 has been pressed\n");
            stamp = 2;
            outputMotorRun.write(HIGH);
            input90Degree.start();
            gotoState(STAMP_SELECTOR_STATE);
        }
        else if (inputButton3.read() == ACTIVE) {
            fdump("Button 3 has been pressed\n");
            stamp = 3;
            outputMotorRun.write(HIGH);
            input90Degree.start();
            gotoState(STAMP_SELECTOR_STATE);
        }
        else if (inputButton4.read() == ACTIVE) {
            fdump("Button 4 has been pressed\n");
            stamp = 4;
            outputMotorRun.write(HIGH);
            input90Degree.start();
            gotoState(STAMP_SELECTOR_STATE);
        }
        break;
        
    case STAMP_SELECTOR_STATE:
        if (input90Degree.read() == ACTIVE) {
            edgeDetect = true;  // We need to make sure we don't count down until the 90 degree sensor has risen *and* fallen
        } else if (input90Degree.read() == NOT_ACTIVE && edgeDetect) {
            edgeDetect = false;                    
            if (--stamp == 0) { // countdown the number of 90 degree sensor hits we've had
                outputCoinDrop.write(HIGH);
                fdump("The penny has been dropped\n");
                outputCounter.write(HIGH);
                countdown = millis();
                gotoState(COIN_DROP_STATE);
            }
        }
        break;
        
    case COIN_DROP_STATE:
        if (millis() > countdown + 1000) { // wait one second after the coin drops to reset the coin drop solenoid
            outputCoinDrop.write(LOW);
            outputCounter.write(LOW);
            gotoState(WAIT_FOR_STAMP_FINISH_STATE);
            countdown = millis();
        }
        break;
        
    case WAIT_FOR_STAMP_FINISH_STATE: // wait five seconds which is enough for the coin to make it through
        if (millis() > countdown + 5 * 1000) {
            gotoState(START_STATE); // Going back to start will wait for the motor to hit Home
        }
        break;                                                          

    case SHUTDOWN_STATE: // not currently used
        outputRedLeverLift.write(LOW);
        outputMotorRun.write(LOW);
        outputCoinDrop.write(LOW);
        outputCounter.write(LOW);        
        gotoState(FOREVER_STATE);
        break;

    case RESET_STATE:
        display.clearDisplay();
        display.setTextSize(2);
        display.setTextColor(WHITE);
        display.setCursor(0,0);
        display.println(F("Reset!"));
        display.display();

        fdump("Resetting board using watchdog...\n");
        Serial.flush();
        
        // enable watchdog timer (which will reboot the board) and wait until it fires
        wdt_enable(WDTO_15MS);
        while (true)
            ;
        break;

    case FOREVER_STATE:
        break;
    }

    // housekeeping for each loop
    updateSerialKeys();
    displayStatus();

    // see if we're supposed to reset
    if (inputReset.read() == ACTIVE) {
        fdump("---Reset initiated---\n");
        gotoState(RESET_STATE);
    }
}


// displayStatus
//  Shows the status of the system on the OLED screen
void displayStatus(void) {
    static unsigned long timeLastStateChange = 0;
    static int lastState = INVALID_STATE;
    
    // time since last state change
    unsigned long timeNow = millis();
    if (theState != lastState) {
        lastState = theState;
        timeLastStateChange = timeNow;
    }
    unsigned long timeSinceLastStateChange = timeNow - timeLastStateChange;

    // after some period, clear the display to save the poor OLED
    if (timeSinceLastStateChange > SCREENSAVER_INTERVAL_MS) {
        display.clearDisplay();
        display.display();
        return;        
    }
    
    display.clearDisplay();
    display.setTextSize(1);
    display.setTextColor(WHITE);
    display.setCursor(0,0);

    // state
    display.println(dumpState(theState));

    // Outputs
    display.setTextSize(2);
    outputRedLeverLift.displayLevel();
    outputMotorRun.displayLevel();
    outputCoinDrop.displayLevel();

    // Inputs
    inputHome.displayLevel();
    input90Degree.displayLevel();
    inputCoinAccept.displayLevel();
    inputButton1.displayLevel();
    inputButton2.displayLevel();
    inputButton3.displayLevel();
    inputButton4.displayLevel();
//    inputReset.displayLevel();h

    display.println();

    display.setTextSize(1);
    display.print("LS: ");
    displayElapsedTime(timeSinceLastStateChange / 1000);
    display.display();
}

// gotoState
//  Transitions to the specified state
//  (and gives us a chance to log the state change)
void gotoState(int newState) {
    fdump("State %s -> %s\n", dumpState(theState), dumpState(newState));
    theState = newState;
}

// dump
//  !!Always use fdump macro (main.h)!!
//  This function is called by the fdump macro and logs a string to both log and to Serial
//  Truncated to 128 characters

void dump(const __FlashStringHelper *fmt, ... ) {
    char buf[128]; // resulting string limited to 128 chars
    va_list args;
    va_start (args, fmt);
    vsnprintf_P(buf, sizeof (buf), (const char *)fmt, args); // progmem for AVR
    va_end(args);
    
    Serial.print(buf);
    theLog.output(buf);
}

// macros from DateTime.h 
#define SECS_PER_MIN  (60UL)
#define SECS_PER_HOUR (3600UL)
#define SECS_PER_DAY  (SECS_PER_HOUR * 24L)

// prepare to compute elapsed time
#define numberOfSeconds(_time_) (_time_ % SECS_PER_MIN)  
#define numberOfMinutes(_time_) ((_time_ / SECS_PER_MIN) % SECS_PER_MIN) 
#define numberOfHours(_time_) (( _time_% SECS_PER_DAY) / SECS_PER_HOUR)
#define elapsedDays(_time_) ( _time_ / SECS_PER_DAY)  

// displayElapsedTime
//  displays elapsed time from number of input seconds
void displayElapsedTime(unsigned long elapsed) {
    int days = elapsedDays(elapsed);
    int hours = numberOfHours(elapsed);
    int minutes = numberOfMinutes(elapsed);
    int seconds = numberOfSeconds(elapsed);

    display.print(days,DEC);  
    printDigits(hours);  
    printDigits(minutes);
    printDigits(seconds);
}

// printDigits
//  Prints decimal digits for elapsed time
void printDigits(byte digits) {
    display.print(F(":"));
    if (digits < 10)
        display.print('0');
    display.print(digits, DEC);  
}

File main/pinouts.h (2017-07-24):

// pinouts.h
//  Pinouts for how the hardware connects to the Arduino
//  July 2017

#ifndef _PINOUT_H
#define _PINOUT_H

// Arduino Inputs
// Pin 0 - NC
// Pin 1 - NC
const int homeSensorPin = 2;
const int degree90SensorPin = 3;
const int coinAcceptPin = 4;
const int button1Pin = 5;
const int button2Pin = 6;
const int button3Pin = 7;
const int button4Pin = 8;
//const int buttonResetPin = 9; // not working, so "disconnect"
const int buttonResetPin = 0;

// Arduino Outputs
const int outputCounterPin = 10;
const int outputCoinDropPin = A1;
const int outputMotorRunPin = 12;
const int outputRedLeverLiftPin = 11;

#endif // #ifndef _PINOUT_H

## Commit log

2017-06-24 Blink easy demo for Arduino
2017-06-24 prints to serial
2017-06-25 first pass at input and output pin definitions
2019-01-21 Corrected/Completed pinout
    Corrected and completed the DB25 connector pin-out, including generic (unused) outputs
2022-03-10 Add files via upload
    STL file for 3D printing a holder for the Arduino and shield for the PennyMan project.
2022-03-12 Add files via upload
    Added latest version of Eagle schematic and board layout files, Bill of Materials, and Zip archive of all manufacturing files (Gerbers, etc.)
    [PennyMan_Ard_R3_Shield_v9.5.brd, PennyMan_Ard_R3_Shield_v9.5.sch]
2022-03-12 Add files via upload
    (not so) Optional display module. Note that the design accommodates either VCC as left-most pin (stuff R4, R5) or GND as left-most pin (stuff R3, R6). This image shows GND on the left-most pin.
2022-03-12 Add files via upload
    First uploaded version of documentation of the Shield board, along with random thoughts on operation and testing of the Shield. Written by David Naegle.
2022-03-12 Add files via upload
    Older versions of schematic and layout files. Note: earlier versions used the MAX chip for debouncing, but it never worked.
    [PennyMan_Ard_R3_Shield_v4a.brd, PennyMan_Ard_R3_Shield_v4a.sch, PennyMan_Ard_R3_Shield_v5.1.brd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]
2022-03-12 Add files via upload
    Latest Shield layout. (This is labeled Ver 4.9 on silkscreen; the latest version that was actually manufactured is Ver 4.8 on the silkscreen).
2022-03-12 Add files via upload
    STL file for mounting Arduino.
    [Arduino_mount1_repaired.stl]
2022-03-12 Add files via upload
    additional documentation, and some explorations for a coin-accept latch mechanism that doesn't require continuous power to a solenoid to keep the machine in a coin-accepting state.

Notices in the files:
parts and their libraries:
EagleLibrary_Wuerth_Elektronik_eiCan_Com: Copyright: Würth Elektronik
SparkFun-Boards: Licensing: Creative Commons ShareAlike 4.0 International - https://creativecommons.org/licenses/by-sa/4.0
